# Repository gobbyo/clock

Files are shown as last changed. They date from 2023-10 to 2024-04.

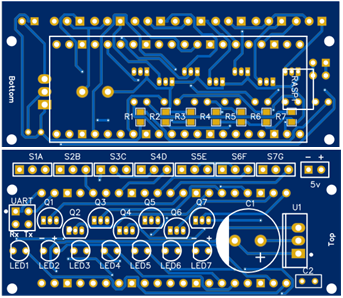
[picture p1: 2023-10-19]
3dprint/images/pcbdigit.png

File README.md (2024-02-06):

# Kinetic Display

The wiki contains all the documentation to get started.

The display was inspired by astroemeria's design found at https://www.instructables.com/Kinetic-Digital-Clock-Arduino-3D-Print/. This Kinetic display is not only a digital clock, but also a date, indoor and outdoor temperature and humidity display. It has a white face and numbers that light when extended. The numbers are made up of segments that extend or retract to display time, date, temperature, and humidity. The display has four digits numbered 0 through 3 with a colon between digit 1 and 2. The colon is made up of two segments, an upper and a lower, which are retracted or extended for time, date, indoor or outdoor temperature and humidity.

https://github.com/gobbyo/clock/assets/6954494/7c7a8180-1fbe-4979-aac9-f4a40820b3cf

Video of the display is located here: https://youtu.be/vFLpjOTYWNc

<!-- You can also view the link to the local version of the ![Kinetic Display Video] -->

displayelements

## Rotating Displays

When configured and running the display rotates time, date, temperature, and humidity each minute.

### Time

The first and last display each minute is time (12 or 24 hour).

illustration-time

**Time is displayed for 30 seconds** each minute from 0 to 15 seconds and from 45 to 60 seconds.

Time displays when the upper and lower colons are EXTENDED. The example shows the time as 12:43 pm when in 24-hour mode, 12:43 AM or PM when in 12-hour mode.  The switch for 12- or 24-hour time is located on the back behind digit 3.

### Month and Day

The second display each minute is the month and day.  Month is displayed on the left face of the display and the day is on the right face.

illustration-date

**Displays for 10 seconds** each minute from 15 to 25 seconds.

Displays when the upper and lower colons are RETRACTED. The example shows the date as December 13, where the month is the left two digits (MM) and the day is the second two digits (DD).  Note the clock face does not have enough digits to include the year along with the month and day.

### Temperature

Indoor and outdoor temperature is the third display each minute.  Indoor and outdoor temperature rotate every two minutes where the first minute is the indoor temperature and the following minute is the outdoor temperature.

illustration-temp

**Displays for 10 seconds** from 25 to 35 seconds.

The INTERIOR temperature displays when the UPPER colon is extended and the lower retracted.  The EXTERIOR temperature displays when the LOWER colon is extended and the upper retracted.  This example shows the INTERIOR temperature as 72° Fahrenheit. Note you can change from Fahrenheit to Celsius using the Admin page.

### Humidity

Indoor and outdoor humidity is the fourth display each minute.  Indoor and outdoor humidity rotate every two minutes where the first minute is the indoor humidity and the following minute is the outdoor humidity.

illustration-humid

**Displays for 10 seconds** from 35 to 45 seconds.

Like temperature, the INTERIOR humidity displays when the UPPER colon is extended and the lower retracted.  The EXTERIOR humidity displays when the LOWER colon is extended and the upper retracted.  This example shows the OUTDOOR humidity as 93%.

<!-- images -->

[displayelements]: https://raw.githubusercontent.com/wiki/gobbyo/clock/media/illustration-display-elements.png
[displayback]: media/illustration-back.png
[illustration-time]: https://raw.githubusercontent.com/wiki/gobbyo/clock/media/illustration-time.png
[illustration-date]: https://raw.githubusercontent.com/wiki/gobbyo/clock/media/illustration-date.png
[illustration-temp]: https://raw.githubusercontent.com/wiki/gobbyo/clock/media/illustration-temp.png
[illustration-humid]: https://raw.githubusercontent.com/wiki/gobbyo/clock/media/illustration-humid.png
[Kinetic Display Video]: https://raw.githubusercontent.com/wiki/gobbyo/clock/media/bluekineticdisplay.mp4

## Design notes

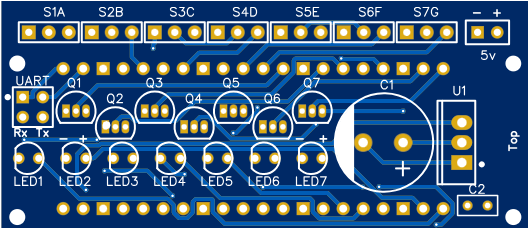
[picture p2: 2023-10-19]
3dprint/images/pcbdigittop.png

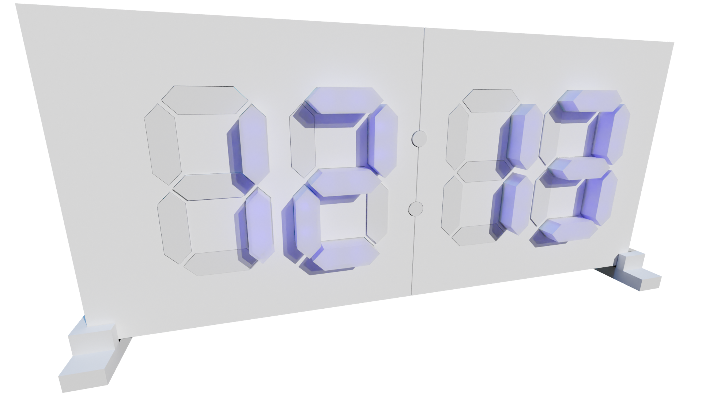
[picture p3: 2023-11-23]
3dprint/images/illustration-date.png

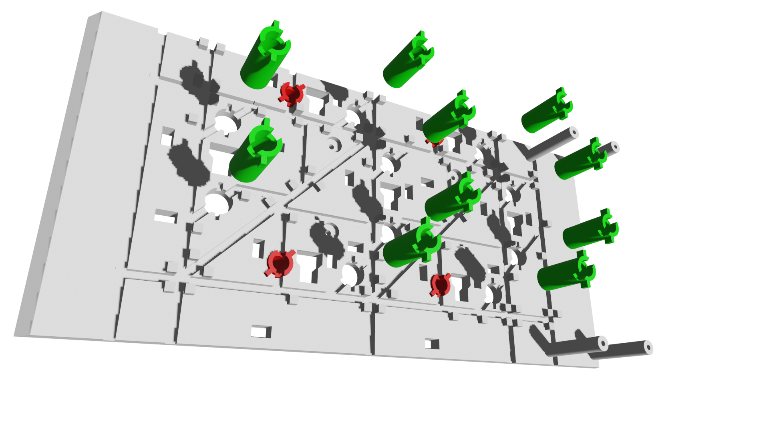
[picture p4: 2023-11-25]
3dprint/images/illustration-back-led1.png

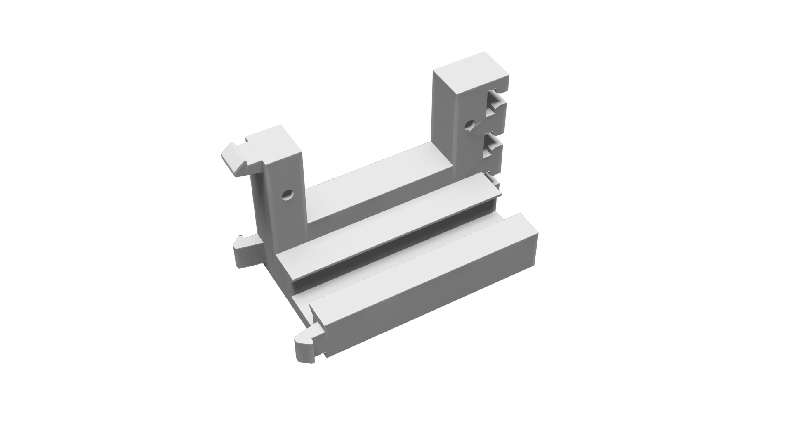
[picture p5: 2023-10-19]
3dprint/images/servoholder.png

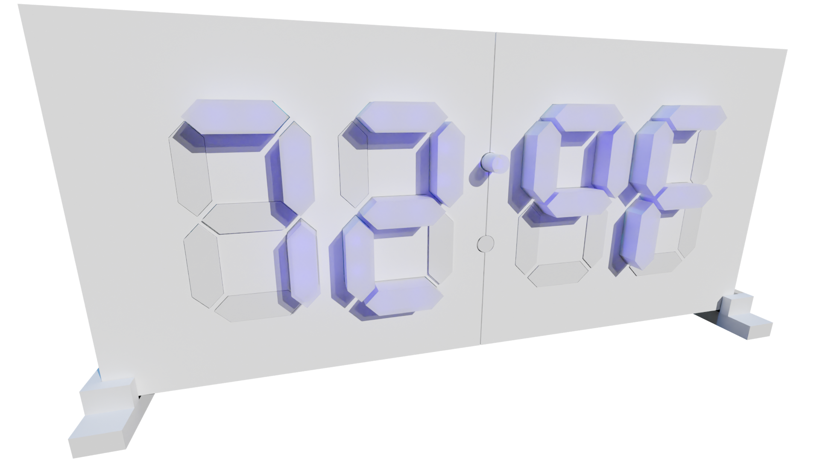
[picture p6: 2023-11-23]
3dprint/images/illustration-temp.png

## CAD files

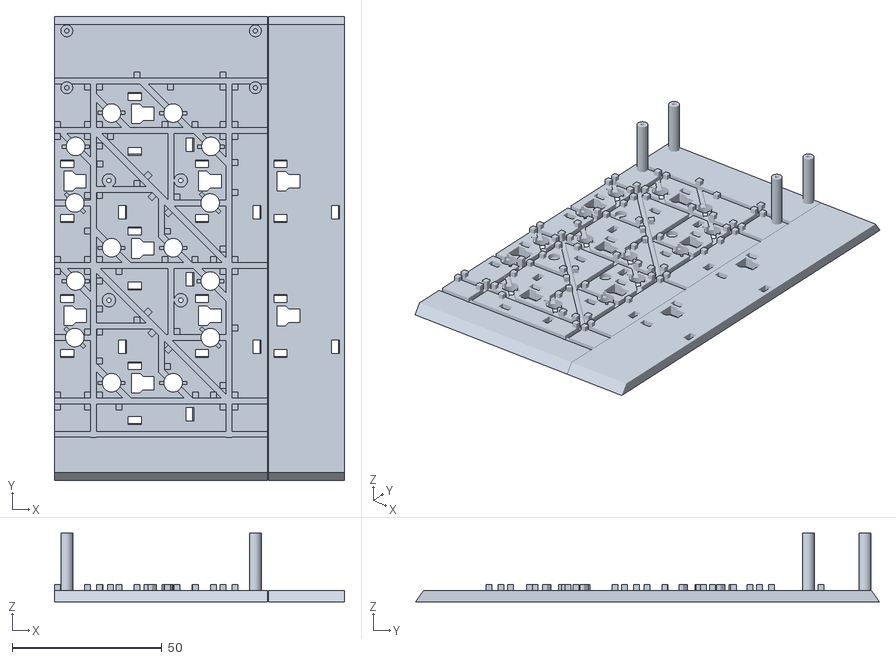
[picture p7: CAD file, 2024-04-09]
3dprint/stl/clock-back3.stl
97.0 x 155.0 x 23.0

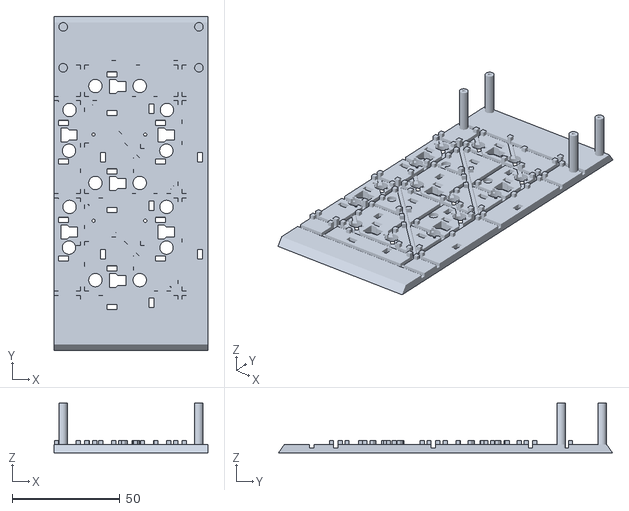
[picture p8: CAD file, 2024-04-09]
3dprint/stl/clock-back2.stl
71.3 x 155.0 x 23.0

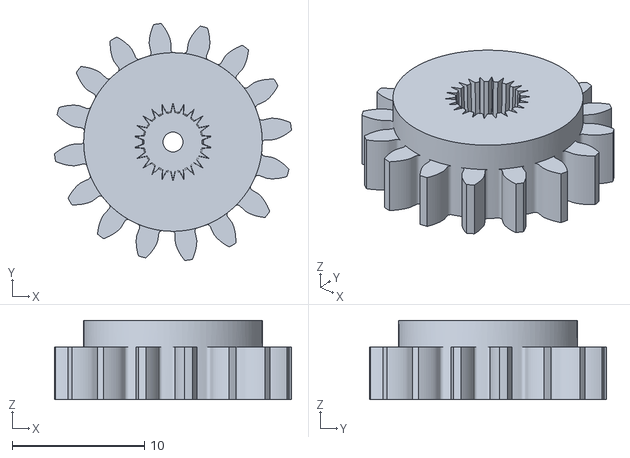
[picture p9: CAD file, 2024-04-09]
3dprint/stl/gear.stl
17.9 x 17.9 x 6.00

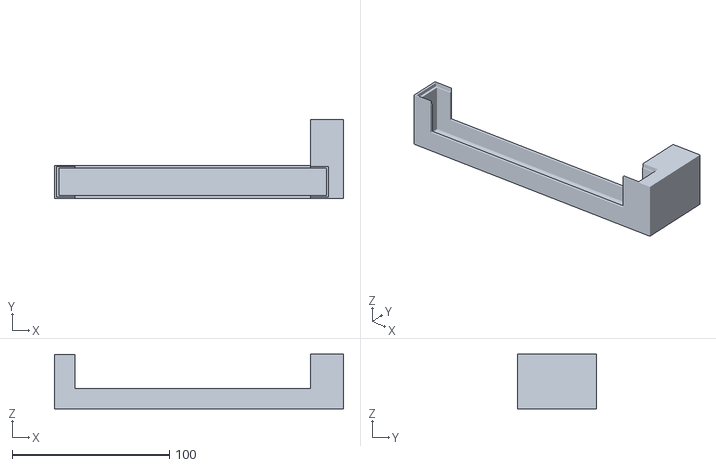
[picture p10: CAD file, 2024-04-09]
3dprint/stl/frame-part-1.stl
184.0 x 50.0 x 35.0

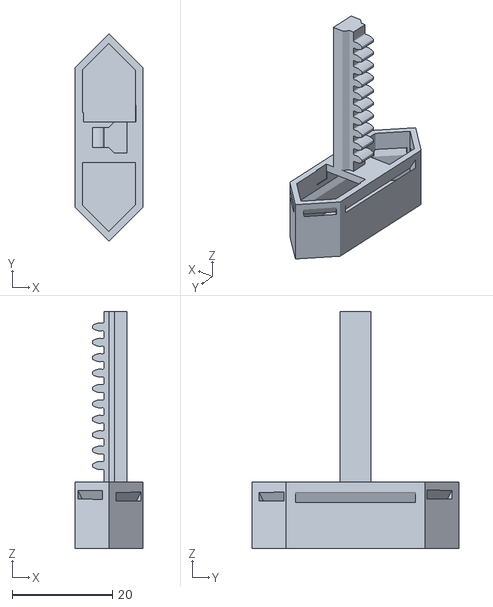
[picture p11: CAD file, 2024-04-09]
3dprint/stl/segment1-part.stl
13.5 x 41.3 x 47.2

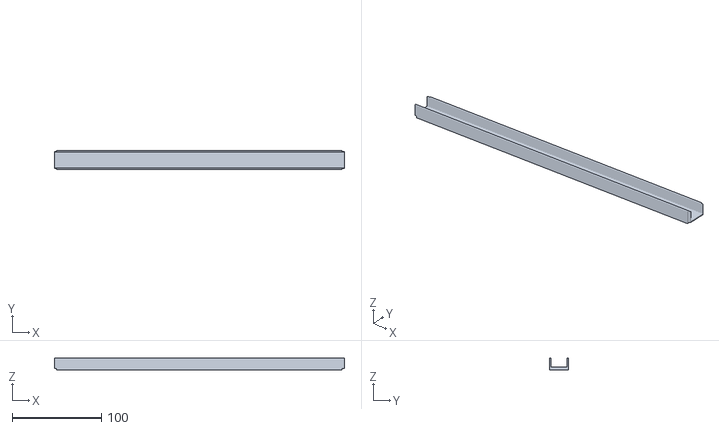
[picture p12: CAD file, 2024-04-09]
3dprint/stl/frame-part-4.stl
325.0 x 21.0 x 13.0

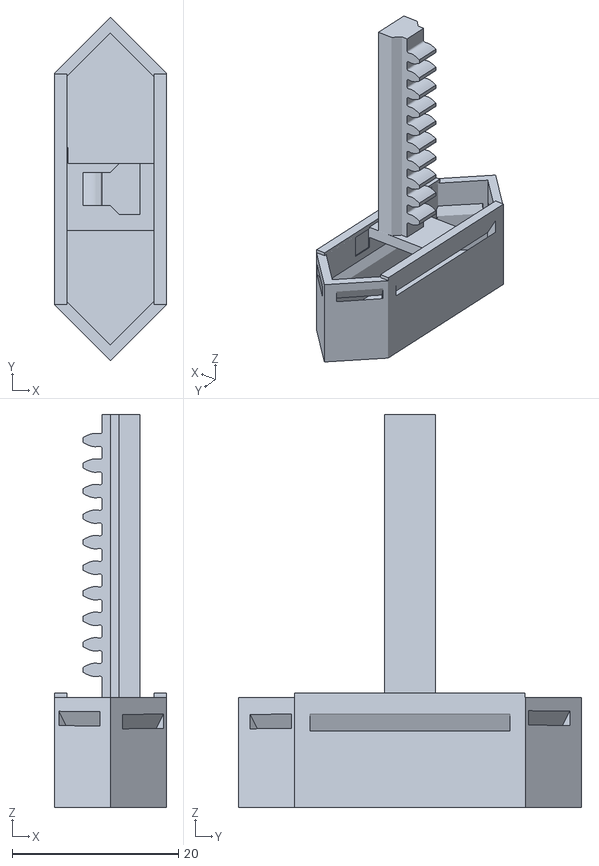
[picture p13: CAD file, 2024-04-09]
3dprint/stl/segment-1.stl
13.5 x 41.3 x 47.2

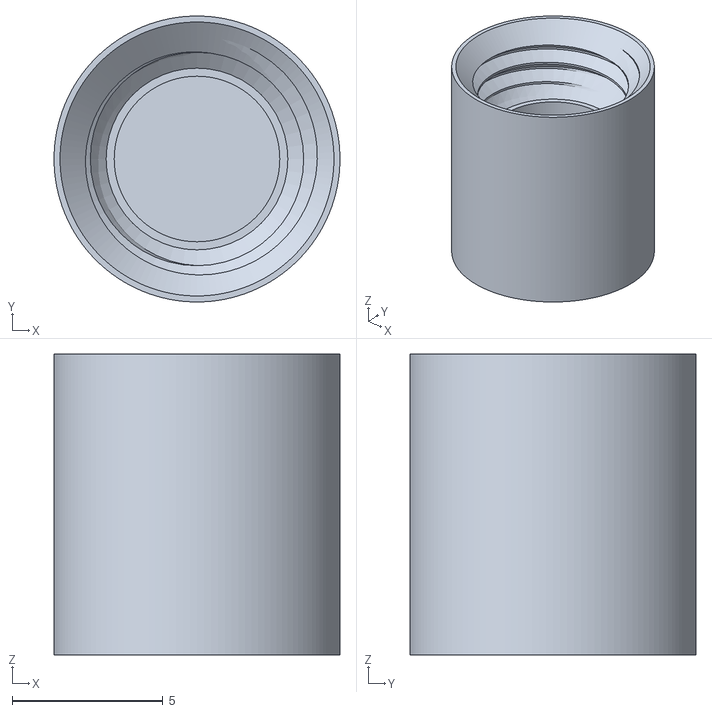
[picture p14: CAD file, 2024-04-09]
3dprint/stl/segment3-part-b.stl
9.50 x 9.50 x 10.0

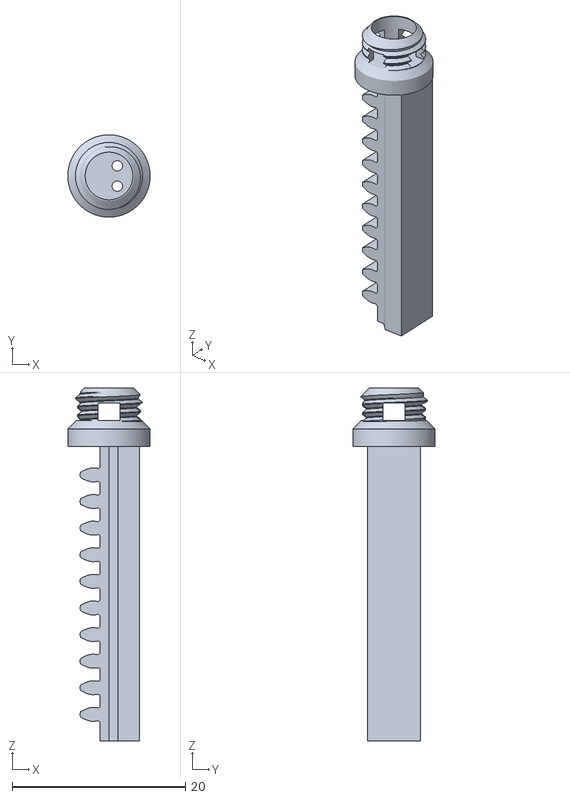
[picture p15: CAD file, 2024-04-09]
3dprint/stl/segment3-part-a.stl
9.50 x 9.50 x 40.7

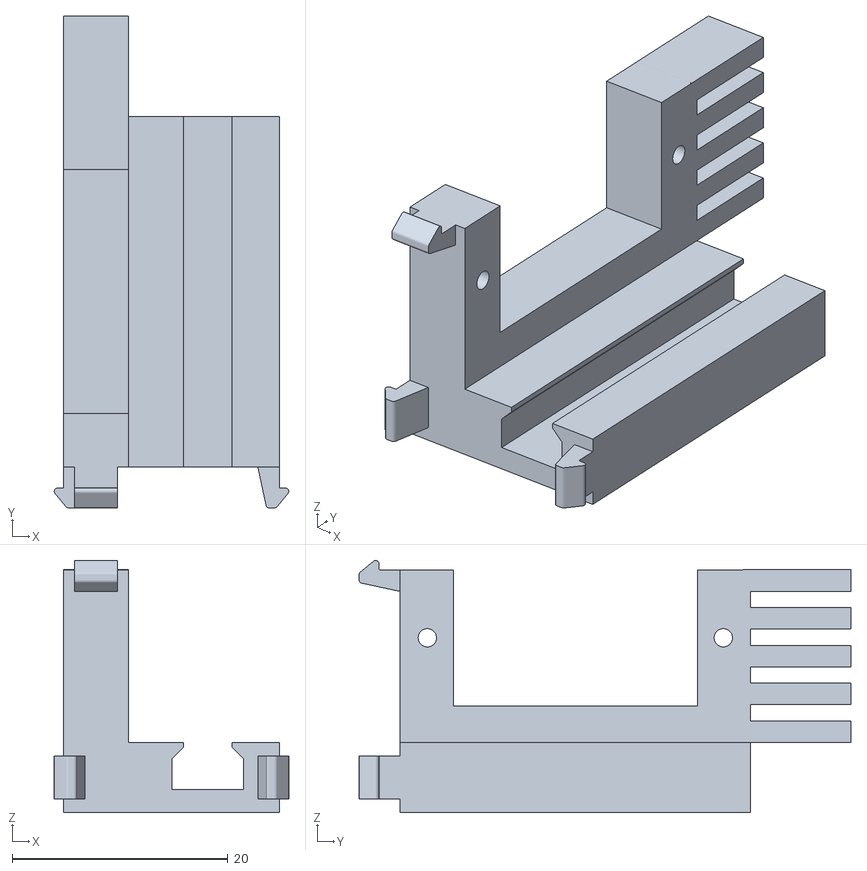
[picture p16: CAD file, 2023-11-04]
3dprint/stl/servoholder.stl
21.7 x 45.6 x 23.4

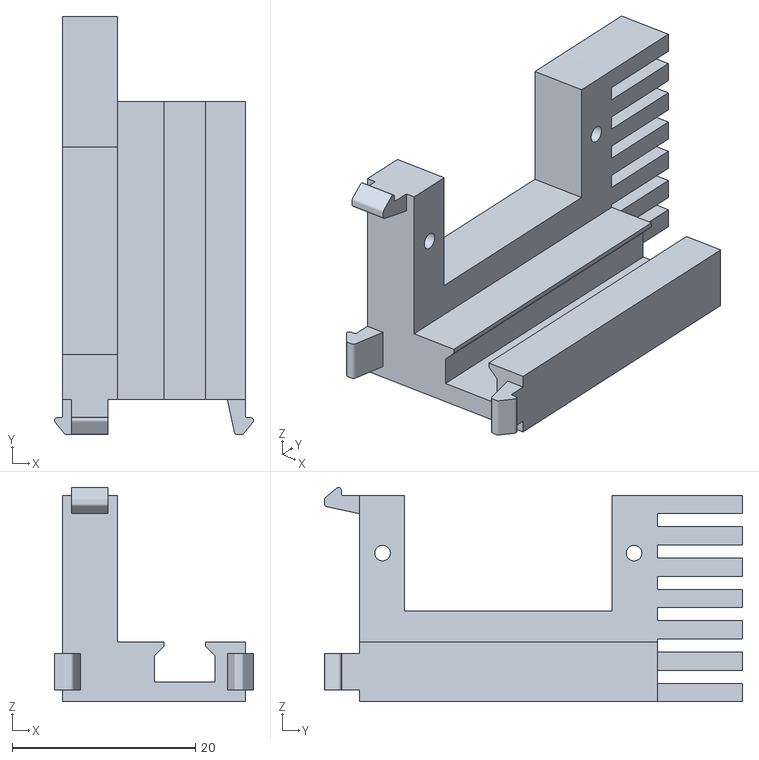
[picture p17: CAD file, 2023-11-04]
3dprint/stl/servoholder-part.stl
21.7 x 45.6 x 23.4

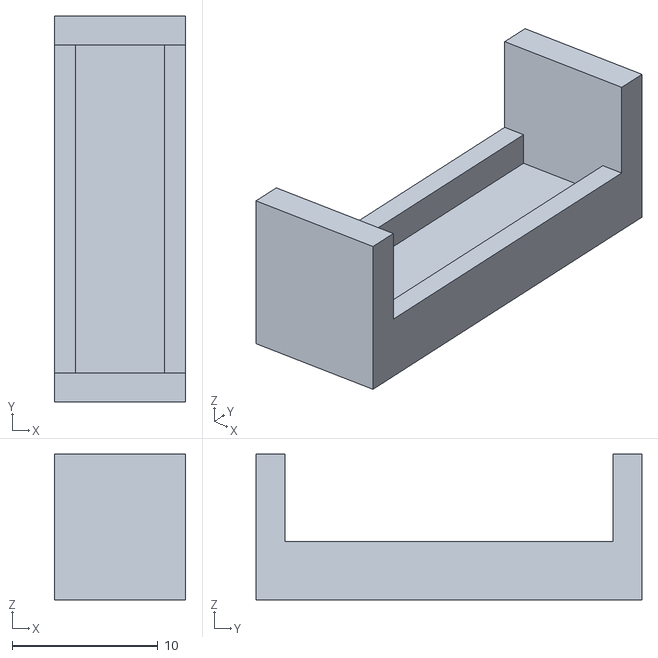
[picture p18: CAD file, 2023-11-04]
3dprint/stl/servoholder-cap-part.stl
9.00 x 26.5 x 10.0

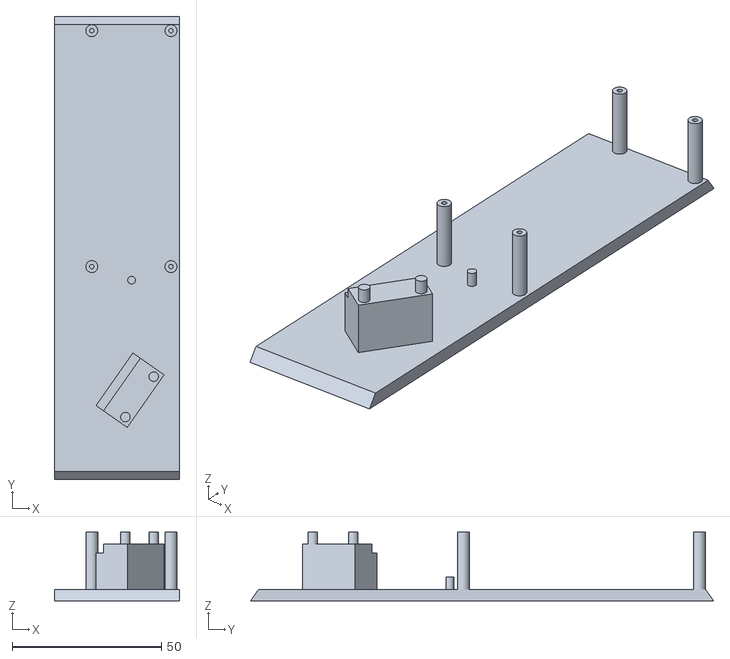
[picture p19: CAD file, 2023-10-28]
3dprint/stl/clock-back1.stl
42.0 x 155.0 x 23.0

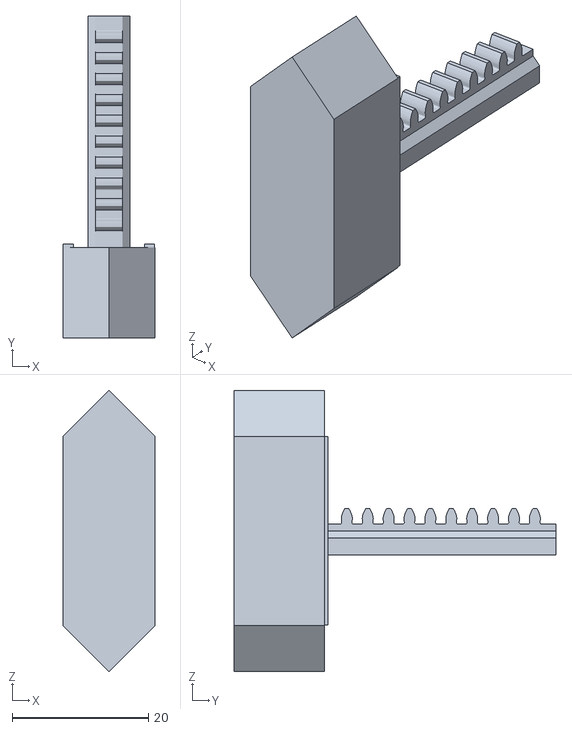
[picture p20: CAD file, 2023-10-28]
3dprint/stl/segment2-plain-part.stl
13.5 x 47.3 x 41.3

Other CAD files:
3dprint/stl/segment2-part.stl
3dprint/stl/segment1-plain-part.stl
3dprint/stl/led1-covered.stl
3dprint/stl/led2-covered.stl
3dprint/blender/clock-back.blend
3dprint/blender/clock-back1.blend
3dprint/blender/clock-back2.blend
3dprint/blender/clock-back3.blend
3dprint/blender/clock-led-part.blend
3dprint/blender/clock-leda-part.blend
3dprint/blender/clock-ledb-part.blend
3dprint/blender/clock.blend
3dprint/blender/clockface-test.blend
3dprint/blender/clockface.blend
3dprint/blender/clockface1.blend
3dprint/blender/clockface2.blend
3dprint/blender/clockstand.blend
3dprint/blender/frame-part-1.blend
3dprint/blender/frame-part-2.blend
3dprint/blender/frame-part-3.blend
3dprint/blender/frame-part-4.blend
3dprint/blender/frame-simple.blend
3dprint/blender/frame.blend
3dprint/blender/gear.blend
3dprint/blender/illustration-back-led1.blend
3dprint/blender/illustration-back-led2.blend
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

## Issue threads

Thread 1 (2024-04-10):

3d print guide

ThEWiZ76, 2024-04-10:
Hi!

First off, great work mate! Thank you for this.
I have read all documentation and files, but couldn't find any clues on the 3d printing stuff. Some parts exist 3 times with slight differences, but it is not clear what to choose. If you could extend the documentation with the differences and how many copies of each part you need, it would be a great help to a lot of people.

Thank you again for your time and effort and sharing it with the community! 👍

JackOrms, 2024-04-11:
Could you maybe include a parts list in general? Including the LED's for inside the segments, circuit components etc etc?

Looking forwards to putting this together!

ThEWiZ76, 2024-04-15:
I decided to do trail and error in the meantime, when complete and functioning I will post it here.

JackOrms, 2024-04-15:
@ThEWiZ76

I am also going to do this & then we can compare notes if needs be.

ThEWiZ76, 2024-04-25:
@JackOrms
I decided to make some changes to the electronics. I use off the shelf boards for the motor controls and leds (pwm) and an esp32 connected to Home Assistant. The boards will be controlled over I2C. I got these parts for **electronics**:

https://www.amazon.nl/dp/B0C6M9LLXR (servo's, 2x 20 pcs)
https://www.amazon.nl/dp/B07CRDCP8V (servo controllers, 2 pcs)
https://www.amazon.nl/dp/B0B5RD9MBR (led controllers, 2 pcs)
https://www.amazon.nl/dp/B0CBX1WYXV (leds 3mm blue)

Still need to find a decent 5V power supply with enough watts, but I may sacrifice an old charger.

I decided to use the sensor data out of Home Assistant as source for the temperature etc, so no need for sensors.

**I printed these parts:**

1x frame-part-1, 2 , 3 and 4

1x clockface1
1x clockface2

1x clock-back1 (modded the Blender file to my needs)
3x clock-back2 (also modded the Blender file)
1x clock-back3 (also modded)

2x segment-3-part-a
2x segment-3-part-b
12x segment-2-part
16x segment-1-part

30x servoholder-part
30x servoholder-cap-part

30x gear

16x led1
40x led2

Printing **done** (finally) so next stop is assembling the servo parts (and test before I connect them to the back plates with this tool: https://www.amazon.nl/dp/B086TSLVV5). And after that getting everything working and tuned!

JackOrms, 2024-04-26:
@ThEWiZ76
Interesting, using off the shelf boards was a good move! I also like the HA integration, it's something I've started playing around with more recently.

You've got further than me, I haven't even started the printing yet... carpet fitted next week and then it can come back out to play/work.

I have however had some PCB's made by a friend using the Gerber files included in the original project & got all of the components fitted to them. Sourcing them was a nightmare but I think I've got it all now. Will confirm once I know it works (or doesn't!).

The file set you have looks good, very similar to what I had selected so that's a sigh of relief.

Regarding the 5V supply, I was planning on using a MeanWell LPV-35-5 that I have on the shelf from a previous project, I think it cost around £12 and is capable of 5A. They also have others ranging from 3A to 12A so should be plenty...

gobbyo, 2024-08-05:
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

I've been redesigning this entire project as the servo approach doesn't last more than 6 to 12 months.  I'll provide all the 3d print details along with links on the new design shortly.

gobbyo, 2024-08-05:
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

When the display is transitioning with the most segments to the "on" position, I recall that it'll burn around 3A.  I've been using a 5v 4A power supply with no issues.

ThEWiZ76, 2024-08-12:
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

Hey, any ETA on that? I have seen on instructables posts about a new design from 5 months ago. It will help me decide to finish this one or wait for the next.

Closed 2024-08-05.

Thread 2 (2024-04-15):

PCB Schematic

hirushiharan, 2024-04-15:
Hi @gobbyo,

Thank you for this repository, excellent work. Additionally, could you please include the schematic of this circuit? Also, if you could elaborate a bit more on the details, it would be helpful.

Thanks & regards,
Hiru

ThEWiZ76, 2024-04-20:
Isn't this what you are looking for? https://github.com/gobbyo/clock/wiki/circuitassembly

hirushiharan, 2024-04-20:
Hi @ThEWiZ76,

Yes, I asked for this. Thanks

Closed 2024-04-20.

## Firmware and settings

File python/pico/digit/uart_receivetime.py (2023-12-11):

#This file is to be uploaded as main.py for each digit 0-3

import machine
from machine import UART, Pin
from servodisplay import servoDigitDisplay
import time
import config
from digitconfigenum import uartCommandEnum
import uarttools
#import logs

waitTime = .1 #second

def updateDigit(digit,conf,displayMotion):
    prev = conf.read("previous")
    digit.setpreviousNumber(prev)
    i = conf.read("current")
    digit.paintNumber(i)
    print("Number {0}".format(i))
    conf.write("previous",i)
    i += 1
    if i >= len(digit._segnum):
        i = 0
    conf.write("current",i)

#TODO: move this to the servodisplay.py class
def rxextend(digit,command,conf,digitNumber):
    print("command to receive extend angles for digit {0} saved in config".format(digitNumber))
    digit._extendAngles = conf.read("extend")
    i = int(command[2])
    value = int(command[3:len(command)])
    digit._extendAngles[i] = value
    conf.write("extend",digit._extendAngles)
    digit.extend(i)

#TODO: move this to the servodisplay.py class
def rxretract(digit,command,conf,digitNumber):
    print("command to receive retract angles for digit {0} saved in config".format(digitNumber))
    digit._retractAngles = conf.read("retract")
    i = int(command[2])
    value = int(command[3:len(command)])
    digit._retractAngles[i] = value
    conf.write("retract",digit._retractAngles)
    digit.retract(i)

#TODO: move this to the servodisplay.py class
def txextend(digit,uart,digitNumber):
    print("send extend angles to controller for digit {0}".format(digitNumber))
    segment = 0
    for angle in digit._extendAngles:
        i = int(angle)
        b = bytearray('{0}{1}{2}{3:03}'.format(digitNumber, uartCommandEnum.txextend, segment,i), 'utf-8')
        uart.write(b)
        print(b)
        time.sleep(.1)
        segment += 1

#TODO: move this to the servodisplay.py class
def txretract(digit,uart,digitNumber):
    print("send retract angles to controller for digit {0}".format(digitNumber))
    segment = 0
    for angle in digit._retractAngles:
        i = int(angle)
        b = bytearray('{0}{1}{2}{3:03}'.format(digitNumber, uartCommandEnum.txretract, segment,i), 'utf-8')
        uart.write(b)
        print(b)
        time.sleep(.1)
        segment += 1

def main():
    conf = config.Config("digit.json")
    extend = conf.read("extend")
    retract = conf.read("retract")
    displayMotion = conf.read("motion")
    digitNumber = conf.read("digit")

    digit = servoDigitDisplay()
    digit.paintNumber(0x0E)

    for i in range(0,7):
        digit._extendAngles[i] = extend[i]
        digit._retractAngles[i] = retract[i]
    
    try:
        uart = UART(0, uarttools.baudRate[0], rx=Pin(uarttools.uartDigitRxPin), tx=Pin(uarttools.uartDigitTxPin), timeout=10)
        uart.init(uarttools.baudRate[0], bits=8, parity=None, stop=1)

        prev = -1

        while True:
            time.sleep(waitTime)
            if uart.any() > 0:
                b = bytearray('000000', 'utf-8')
                uart.readinto(b)
                d = str(b.decode('utf-8'))
                print("uarttools.validate({0}) = {1}".format(d,uarttools.validate(d)))
                if uarttools.validate(d):
                    print("Command = {0}".format(uarttools.decodeHex(d[1])))
                    command = int(uarttools.decodeHex(d[0]))
                    if (command == 4) or (command == digitNumber):
                        command = int(uarttools.decodeHex(d[1]))
                        if (command == uartCommandEnum.time):
                            print("command to display value for digit {0}".format(digitNumber))
                            n = int(uarttools.decodeHex(d[digitNumber+2]))
                            if prev != n:
                                conf.write("current",n)
                                updateDigit(digit,conf,displayMotion)
                                prev = n
                        if (command == uartCommandEnum.rxextend): #receive extend angle
                            rxextend(digit,d,conf,digitNumber)
                        if (command == uartCommandEnum.txextend): #send all extend angles
                            txextend(digit,uart,digitNumber)                        
                        if (command == uartCommandEnum.rxretract): #receive retract angle
                            rxretract(digit,d,conf,digitNumber)
                        if (command == uartCommandEnum.txretract): #send all retract angles
                            txretract(digit,uart,digitNumber)
                        if (command == uartCommandEnum.motion):
                            print("writing to config, 'motion' = {0}".format(uarttools.decodeHex(d[5])))
                            displayMotion = int(uarttools.decodeHex(d[5]))
                            conf.write("motion",displayMotion)
                        if (command == uartCommandEnum.current):
                            print("writing to config, 'current' = {0}".format(uarttools.decodeHex(d[5])))
                            conf.write("current",int(uarttools.decodeHex(d[5])))
                        if (command == uartCommandEnum.previous):
                            print("writing to config, 'previous' = {0}".format(uarttools.decodeHex(d[5])))
                            conf.write("previous",int(uarttools.decodeHex(d[5])))
                        if (command == uartCommandEnum.hybernate):
                            print("hybernate")
                            n = int(uarttools.decodeHex(d[digitNumber+2]))
                            machine.deepsleep(n * 1000)
                            machine.reset()
                        if (command == uartCommandEnum.timedhybernation):
                            print("timed hybernation")
                            n = int(d[2:6]) * 60
                            conf.write("timedhybernation", n)
                            machine.deepsleep(n * 1000)
                        if (command == uarttools.decodeHex(uartCommandEnum.reset)):
                            print("reset")
                            digit.paintNumber(0x0E)
                            conf.write("current",0)
                            conf.write("previous",14)
                            machine.reset()
    except KeyboardInterrupt:
        print('KeyboardInterrupt')
    finally:
        conf.write("current",0)
        conf.write("previous",14)
        digit.__del__()
        print('Done')
if __name__ == "__main__":
    main()

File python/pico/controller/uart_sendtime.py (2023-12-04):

# Filename: main.py
# Author: Jeff Beman
# Date: summer 2023
# This file is saved as main.py and uploaded onto the Pico W display controller
# This is the main entry point to the controller for the Kinetic Display
# All the files under the common folder are shared between the controller and the
# digit controllers.  The files under the controller folder are specific to the
# controller and the files under the digit folder are specific to the digit controllers.

import kineticDisplay
import time
import config
from timeEnum import timeEnum
from scheduler import schedule, scheduleEnum

# Main entry point for the controller
# This is the main loop that runs the display
# It is responsible for checking the time and updating the display
# It is also responsible for checking the state of the switch and the time, 
# putting the display into hybernation mode, checking the schedule and updating the display
# Note the code makes heavy use of the config file to store and retrieve state information
# in the event there is an unexpected power loss
def main():
    conf = config.Config("config.json")
    display = kineticDisplay.kineticDisplay(conf)

    try:
        display.admin()
        if display.connectWifi():
            display.syncClock()
        
        display.setIndoorTemp(conf)
        display.setOutdoorTemp(conf)

        itinerary = schedule()
        lastMinute = 0
        lastHour = 0

        while True:
            elapsedSeconds = round(display._sync.rtc.datetime()[timeEnum.seconds])
            elapsedMinutes = round(display._sync.rtc.datetime()[timeEnum.minutes])
            elapsedHours = round(display._sync.rtc.datetime()[timeEnum.hours])
            print("elapsed {0}:{1}:{2}".format(elapsedHours, elapsedMinutes, elapsedSeconds))
            #check state of switch
            display.hybernateSwitch(conf)
            #check state of time
            display.hybernateTime(conf)

            if elapsedMinutes != lastMinute:
                itinerary.initSecondSchedule()
                lastMinute = elapsedMinutes
                print("initSecondSchedule()")

            if elapsedHours != lastHour:
                itinerary.initMinuteSchedule()
                lastHour = elapsedHours
                print("initMinuteSchedule()")
            
            if itinerary.secondsSchedule[elapsedSeconds] == scheduleEnum.time:
                display.displayTime(display._sync)
                itinerary.clearNearFutureDuplicates(itinerary.secondsSchedule, elapsedSeconds, scheduleEnum.time)
                print("elapsed {0}:{1}:{2}".format(elapsedHours, elapsedMinutes, elapsedSeconds))

            if itinerary.secondsSchedule[elapsedSeconds] == scheduleEnum.date:
                display.displayDate()
                itinerary.clearNearFutureDuplicates(itinerary.secondsSchedule, elapsedSeconds, scheduleEnum.date)
                print("elapsed {0}:{1}:{2}".format(elapsedHours, elapsedMinutes, elapsedSeconds))

            if itinerary.secondsSchedule[elapsedSeconds] == scheduleEnum.temp:
                display.displayTemp(conf)
                itinerary.clearNearFutureDuplicates(itinerary.secondsSchedule, elapsedSeconds, scheduleEnum.temp)
                print("elapsed {0}:{1}:{2}".format(elapsedHours, elapsedMinutes, elapsedSeconds))

            if itinerary.secondsSchedule[elapsedSeconds] == scheduleEnum.humid:
                display.displayHumidity(conf)
                itinerary.clearNearFutureDuplicates(itinerary.secondsSchedule, elapsedSeconds, scheduleEnum.humid)
                print("elapsed {0}:{1}:{2}".format(elapsedHours, elapsedMinutes, elapsedSeconds))
            
            if itinerary.minutesSchedule[elapsedMinutes] == scheduleEnum.updateClock:
                print("--updating display--")
                if display.connectWifi():
                    display.syncClock()
                itinerary.minutesSchedule[elapsedMinutes] = -1
                print("elapsed {0}:{1}:{2}".format(elapsedHours, elapsedMinutes, elapsedSeconds))

            if itinerary.minutesSchedule[elapsedMinutes] == scheduleEnum.updateIndoor:
                print("--reading indoor temp sensor--")
                display.setIndoorTemp(conf)
                itinerary.minutesSchedule[elapsedMinutes] = -1
                print("elapsed {0}:{1}:{2}".format(elapsedHours, elapsedMinutes, elapsedSeconds))

            if itinerary.minutesSchedule[elapsedMinutes] == scheduleEnum.updateOutdoor:
                print("--reading outdoor temp sensor--")
                display.setOutdoorTemp(conf)
                itinerary.minutesSchedule[elapsedMinutes] = -1
                print("elapsed {0}:{1}:{2}".format(elapsedHours, elapsedMinutes, elapsedSeconds))
            
            time.sleep(1)

    except KeyboardInterrupt:
        print('KeyboardInterrupt')
    finally:
        display.__del__()
        print('Done')

if __name__ == "__main__":
    main()

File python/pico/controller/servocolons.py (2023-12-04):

# Filename: servocolons.py
# Author: Jeff Beman
# Date: summer 2023

from machine import Pin
from servo import sg90
import config
import time

# The servoColonsDisplay class is used by the main Pico W to control 
# the colons on the kinetic display
class servoColonsDisplay:
    _segpins = [2,3] # upper, lower
    _switchpins = [9,10] #upper, lower
    _ledpins = [16,17] #upper, lower
    #TODO: make the extend and retract angles configurable
    _extendAngles = [20,20]
    _retractAngles = [110,110]
    _rateofmovement = 3 #degrees
    _servospeed = 0.03 #default servo speed
    _servowait = 0.4
    _switches = []
    _servos = []    
    _leds = []
    _config = None

    def __init__(self, conf):
        print("servoColonsDisplay constructor")
        self._config = conf
        colonstate = self._config.read("colonstate")

        for i in self._segpins:
            self._servos.append(sg90(i))
        for i in self._switchpins:
            self._switches.append(Pin(i, Pin.OUT))
        for i in range(0,len(self._ledpins)):
            self._leds.append(Pin(self._ledpins[i], Pin.OUT))
            if colonstate[i]:
                self._leds[i].on()
            else:
                self._leds[i].off()

    def __del__(self):
        for led in self._leds:
            led.off()
        for i in range(0, 2):
            self._servos[i].move(self._retractAngles[i])
            print("servo {0} move {1}".format(i,self._retractAngles[i]))
            i += 1
        print("servoColonsDisplay destructor")

    # This method is used to extend the colons
    # The colons are extended one segment at a time
    # Note that the configuration file is used to store the state of the colons
    # in the event there is an unexpected power loss
    def extend(self, upper, lower):
        colonstate = self._config.read("colonstate")
        print("extend colons, colonstate={0}".format(colonstate))
        for i in range(0,2):
            if ( i == 0 and upper == True) or (i == 1 and lower == True):
                if not colonstate[i]:
                    self._switches[i].on()
                    print("extend {0} move {1}".format(i,self._extendAngles[i]))
                    self._servos[i].move(self._extendAngles[i])
                    time.sleep(self._servowait)
                    self._switches[i].off()
                    self._leds[i].on() # turns on AFTER the servo extends the segment
                    colonstate[i] = True
        self._config.write("colonstate",colonstate)

    # This method is used to retract the colons
    # The colons are retracted one segment at a time
    # Note that the configuration file is used to store the state of the colons
    # in the event there is an unexpected power loss
    def retract(self, upper, lower):
        colonstate = self._config.read("colonstate")
        print("retract colons, colonstate={0}".format(colonstate))
        for i in range(0,2):
            if (i == 0 and upper == True) or (i == 1 and lower == True):
                if colonstate[i]:
                    self._leds[i].off() # turns off BEFORE the servo retracts the segment
                    self._switches[i].on() 
                    print("retract {0} move {1}".format(i,self._retractAngles[i]))
                    self._servos[i].move(self._retractAngles[i])
                    time.sleep(self._servowait)
                    self._switches[i].off()
                    colonstate[i] = False
        self._config.write("colonstate",colonstate)

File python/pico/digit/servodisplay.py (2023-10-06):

from machine import Pin
from servo import sg90
import time

class servoDigitDisplay:
    _segpins = [2,3,4,5,6,7,8] # a,b,c,d,e,f,g
    _switchpins = [9,10,11,12,13,14,15]
    _ledpins = [16,17,18,19,20,21,22]
    _extendAngles = [0,0,0,0,0,0,0]
    _retractAngles = [90,90,90,90,90,90,90]
    _rateofmovement = 3 #degrees
    _servospeed = 0.01 #default servo speed
    _servowait = 0.4
    # 0 = 	0011 1111   0x3F
    # 1 =	0000 0110   0x06
    # 2 =	0101 1011   0x5B
    # 3 =	0100 1111   0x4F
    # 4 =	0110 0110   0x66
    # 5 =	0110 1101   0x6D
    # 6 =	0111 1101   0x7D
    # 7 =	0000 0111   0x07
    # 8 =   0111 1111   0x7F
    # 9 =   0110 0111   0x67
    # A =   0110 0011   0x63  #degrees
    # B =   0101 1100   0x5C  #percent
    # C =   0011 1001   0x39  #celcius
    # D =   0111 0001   0x71  #farhenheit
    # E =   0000 0000   0x00  #clear
    # F =   1000 0000   0x00  #ignore
    _segnum = [0x3F,0x06,0x5B,0x4F,0x66,0x6D,0x7D,0x07,0x7F,0x67,0x63,0x5C,0x39,0x71,0x00]
    _switches = []
    _servos = []    
    _leds = []
    _clearRegister = [0,0,0,0,0,0,0,0]
    _previousNumber = _clearRegister

    def __init__(self):
        #print("servoDigitDisplay constructor")
        for i in self._segpins:
            self._servos.append(sg90(i))
        for i in self._switchpins:
            self._switches.append(Pin(i, Pin.OUT))
        for i in range(0,len(self._ledpins)):
            self._leds.append(Pin(self._ledpins[i], Pin.OUT))
            self._leds[i].off()

    def __del__(self):
        self.paintFastNumber(0x0E)
        for led in self._leds:
            led.off()
        print("servoDigitDisplay destructor")

    def extend(self,index):
        print("extend {0}".format(index))
        i = self._retractAngles[index]
        self._switches[index].on()
        self._servos[index].move(self._extendAngles[index])
        time.sleep(self._servowait)
        self._switches[index].off()
        self._leds[index].on()

    def retract(self,index):
        print("retract {0}".format(index))
        self._leds[index].off()
        i = self._extendAngles[index]
        self._switches[index].on() 
        self._servos[index].move(self._retractAngles[index])
        time.sleep(self._servowait)
        self._switches[index].off()

    def getArray(self,val):
        a = [0,0,0,0,0,0,0,0]
        i = 0
        for s in a:
            a[i] = (val & (0x01 << i)) >> i
            i += 1
        return a
    
    def setpreviousNumber(self,val):
        self._previousNumber = self.getArray(self._segnum[val])
        for i in range(0,len(self._previousNumber)):
            if self._previousNumber[i] == 1:
                self._leds[i].on()

    def paintFastNumber(self,val):
        input = []
        input = self.getArray(self._segnum[val])
        print("paintNumber._previousNumber {0}".format(self._previousNumber))

        for i in range(0,len(input)):
            if input[i] == 1:
                if self._previousNumber[i] == 0:
                    self.extend(i)           
            if input[i] == 0:
                if self._previousNumber[i] == 1:
                    self.retract(i)

        self._previousNumber = input
    
    def paintSlowNumber(self,val):
        current = []
        current = self.getArray(self._segnum[val])
        result = [-1,-1,-1,-1,-1,-1,-1]

        for i in range(0,len(current)):
            t = self._previousNumber[i] + current[i]
            if not (t == 0 or t == 2):
                result[i] = current[i]

        extendAngles = self._extendAngles.copy()
        retractAngles = self._retractAngles.copy()

        #Start change of digit, turn on power for servos, turn off LEDs
        for i in range(0,len(result)):
            self._switches[i].on()
            if result[i] == 1:
                #print("extend start {0}".format(i))
                self._leds[i].off()
            if result[i] == 0:
                #print("retract start {0}".format(i))
                self._leds[i].off()

        #Move segments to change digit
        end = round(90/self._rateofmovement)

        for e in range(end):
            print("e={0} of end={1}".format(e,end))
            for i in range(len(result)):
                if result[i] == 1:
                    retractAngles[i] -= self._rateofmovement
                    if retractAngles[i] >= self._extendAngles[i]:
                        #print("{0} extend angle = {1}".format(i, retractAngles[i]))
                        self._servos[i].move(retractAngles[i])
                if result[i] == 0:
                    extendAngles[i] += self._rateofmovement
                    if extendAngles[i] <= self._retractAngles[i]:
                        #print("{0} retract angle = {1}".format(i, extendAngles[i]))
                        self._servos[i].move(extendAngles[i])
                time.sleep(self._servospeed)

        for i in range(len(result)):
            self._switches[i].off()

        #Finish moving segments, turn off power to servos, turn on LEDs
        for i in range(len(result)):
            self._switches[i].on()
            if result[i] == 1:
                self._servos[i].move(extendAngles[i]) #finish any leftover
                time.sleep(.2)
            if result[i] == 0:
                self._servos[i].move(retractAngles[i]) #finish any leftover
                time.sleep(.2)
            
        for i in range(len(result)):
            self._switches[i].off()
            if result[i] == 1:
                self._leds[i].on()
            if result[i] == 0:
                self._leds[i].off()
        self._previousNumber = current

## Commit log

2023-07-18 updated display
    [back-2 (1).stl, back.stl, clock.blend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]
2023-07-18 added uart test files
2023-07-18 added uart transmit and receive
2023-07-19 initial drafts of circuitry
    [segment1-part.blend, segment1-part.stl, segment1.blend]
2023-07-21 updated clock parts to include LEDs.
    [clock-back-part.blend, clock-back-part.stl, clock-led-part.blend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]
2023-07-21 improved segments in 3d print files to include LEDs
    [segment.blend, segment1-part.blend, segment1-part.stl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]
2023-07-24 updated code to improve receive times and servo display
    [segment.blend, segment1-part.blend, segment1-part.stl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]
2023-08-01 updated servos to avoid speed control
    [servodisplay.py, uart_receivetime.py, uart_sendtime.py]
2023-08-01 added servo wait time before shutting it off
2023-08-03 Updated for 3d printing added gerber files for PCB.
    [clock-back-part.blend, clockface.blend, segments.blend]
2023-08-13 added pico w hotspot
2023-08-13 interim checkin
    [clock-back-part.blend, clock-back-part.stl]
2023-08-16 updated working checking
    [clock.xlsx, servoholder.blend, servoholder.stl]
2023-08-16 added config file, removed creds from file
    [segment1-part.blend, segment1-part.stl, segment2-part.blend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]
2023-08-16 updated config code
    [clock-back-part-b.stl, clock-back-part.blend, clock.blend]
2023-08-18 tweaked 3d prints
    [clock-back-part.blend, clock.blend, segment1-part.blend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]
2023-08-21 added temperature and humidity sensor detection
    [clock-back-part.blend, clock-back-part.stl, clock.blend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]
2023-08-28 updated gerber file
2023-09-05 added code to reduce power consumption
    [clock-back-part.stl, clock-back2-part.blend, clock-back2-part.stl]
2023-09-12 added logging
    [back-2.stl, face-1.stl]
2023-09-12 fixed bugs in send and receive time
    [testservodigit.py, uart_receivetime.py, uart_sendtime.py]
2023-09-14 updated design to light clock colon
    [segment.blend, segment3-part.blend, segment3-part.stl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]
2023-09-14 updated frequency to read sensor and internet
2023-09-19 added colons to clock
    [clockstand.blend, clockstand.stl]
2023-09-19 refactored sendtime, fixed servo colon bug
    [servocolons.py, singleservotest.py, uart_sendtime.py]
2023-09-19 refactored kineticClock class, fixed bug saving externalIPAddress in syncRTC
    [syncRTC.py, uart_sendtime.py]
2023-09-20 updated print and config
2023-09-23 fixed wifi scheduling bug problem
    [servocolons.py, uart_sendtime.py]
2023-09-23 updated timing for restricted power situations
2023-09-25 created a frame and stand
    [clock-back-part.blend, frame-part-1.blend, frame-part-1.stl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]
2023-09-28 updated frame, cleaned up scheduling code
    [frame-part-1.blend, frame-part-1.stl, frame-part-2.blend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]
2023-09-28 reorganized code heirarchy, broke out classes to separate files
    [scheduler.py, singleservotest.py, testservodigit.py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]
2023-09-29 fixed bug with changing temp from c to f
    [servodisplay.py]
2023-10-02 updated colon model and code
    [frame-part-1.blend, frame-part-1.stl, frame-part-2.blend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]
2023-10-03 updated cicuitry and reflected it in code
    [segment3-part-a.blend, segment3-part-a.stl, segment3-part-b.blend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]
2023-10-03 Files no longer needed
    [segments-test.blend]
2023-10-06 updated circuit and code for hybernation
2023-10-09 refactored hybernation logic
    [clock-back-part.blend]
2023-10-11 updated design of clock face and back
    [clock-back-part-b.stl, clock-back-part.blend, clock-back-part.stl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]
2023-10-12 restructured code layout
    [back-2.stl, back.stl, clock-back.blend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]
2023-10-19 updated pcbs, updated clock design, added illustrations
    [clock-back.blend, clock-back1.blend, clock-back1.stl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]
2023-10-23 updated stl for enclosed LED casing, added web admin functionality
    [clock-back1.stl, illustration-clock-back3.blend, illustration-clockface1.blend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]
2023-10-28 updated wifi
    [clock-back.blend, clock-back1.blend, clock-back1.stl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]
2023-11-04 created mechanisms to adjust segment angles from controller
    [servoholder-cap-part.blend, servoholder-cap-part.stl, servoholder-part.blend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]
2023-11-04 removed temp files
    [clock.xlsx]
2023-11-08 fixed bug with uart
    [config.py, digitconfigenum.py, servo.py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]
2023-11-15 updated pcbs, updated uart
2023-11-23 added getting started instructions
    [frame-simple.blend, illustration-segment.blend, segment2-plain-part.blend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]
2023-11-25 updated documentation, refactoring controller classes
    [clock-back2.blend, illustration-back-led1.blend, illustration-back-led2.blend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]
2024-04-09 updated controller and digit pcbs
    [clock-back2.stl, clock-back3.stl, frame-part-1.stl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]
